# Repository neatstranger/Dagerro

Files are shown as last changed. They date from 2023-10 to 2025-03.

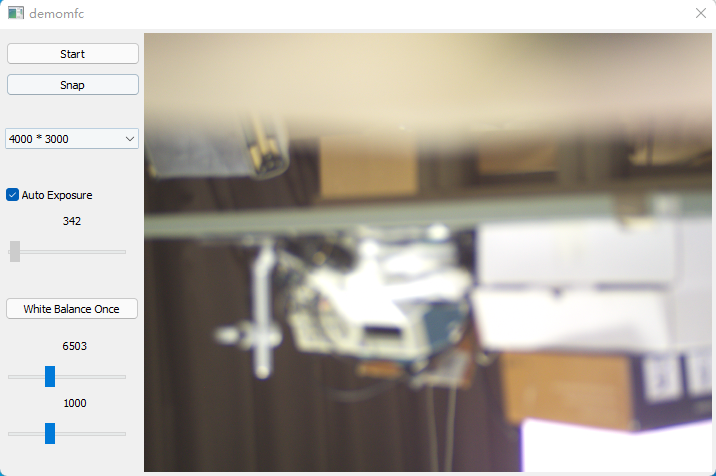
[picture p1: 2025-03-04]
toupcam/raw_sdk/doc/images/demomfc.png

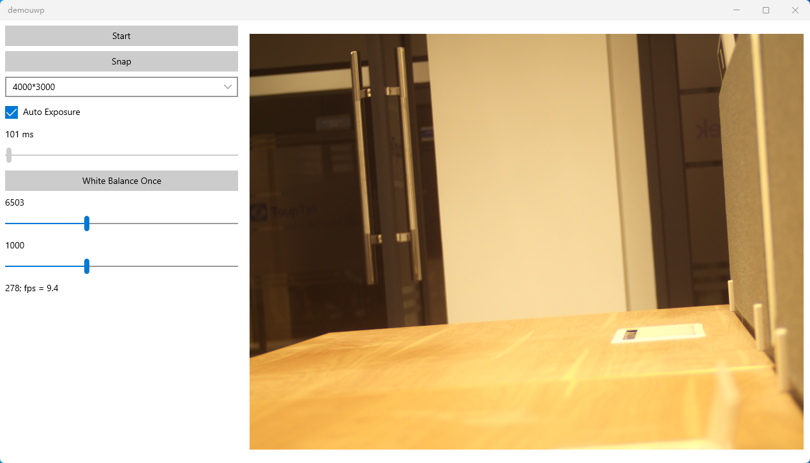
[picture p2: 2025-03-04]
toupcam/raw_sdk/doc/images/demouwp.png

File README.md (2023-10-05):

# Dagerro
>The first known attempt at astronomical photography was by Louis Jacques Mandé Daguerre, inventor of the daguerreotype process which bears his name, who attempted in 1839 to photograph the Moon. Tracking errors in guiding the telescope during the long exposure meant the photograph came out as an indistinct fuzzy spot. [Source](https://en.wikipedia.org/wiki/Astrophotography#:~:text=The%20first%20known%20attempt%20at,as%20an%20indistinct%20fuzzy%20spot.)

# Guide Timing
Some notes for myself as well as anyone reading. 
We need to move the steppers about 8 times per second and the Real Time Clock(RTC) doesn't allow for time resolution greater than 1 second. 
The RTC(DS3231) outputs 32,768 pulses per second on the 32K pin. We attach an interrupt to that pin with the following line.

`attachInterrupt(digitalPinToInterrupt(interruptPin), countCycles, CHANGE);`

Note the use of the `CHANGE` for activation. This means that we will capture one interrupt for each rise, and one for each fall.
With our second now divided up into 65,536 segments.

```
1 Degree = 60 ArcMinutes
1 ArcMinute = 60 ArcSeconds
1 Degree = 3600 ArcSeconds
```

How fast does the earth rotate? My previous assumption of ~1ArcSecond/Second~ is wrong. Let's do the math.
```
360° = 24 Hours
15° = 1 Hour or 60 Minutes or 3600 Seconds
1° or 3600 ArcSeconds = 4 Minutes or 240 Seconds
Math = 3600(ArcSeconds-Angle)/240 (Seconds-Time)
15 ArcSeconds(Angle) = 1 Second(Time)

```

The arduino receive exactly 1,658,880 pulses every 25.3125 seconds.
During this period of time, we need to take exactly 1500 steps.

python function to solve the problem.

```
x = 1
maxcount = 1500
xmult = 1105
ymult = 1107

while x <= maxcount:
    y = maxcount - x
    if (xmult*x)+(ymult*y) == 1658880:
        print(x)
        print(y)
        print((xmult*x) + (ymult*y))
    x+=1
```
I used this script, changing the values for xmult and ymult, until I got a result that looks like this:

```
810
690
1658880

```
Which means that if we take a step every 1105 interrupts, 810 times.
Followed by taking a step every 1107 interrupts, 690 times. 
We will have taken 1500 steps in exactly 25.3125 seconds. 

```
1500 Steps * 0.253125 ArcSeconds Per Step = 379.6875 ArcSeconds
379.6875 ArcSeconds / 25.3125 Seconds
15 ArcSeconds / Second
```

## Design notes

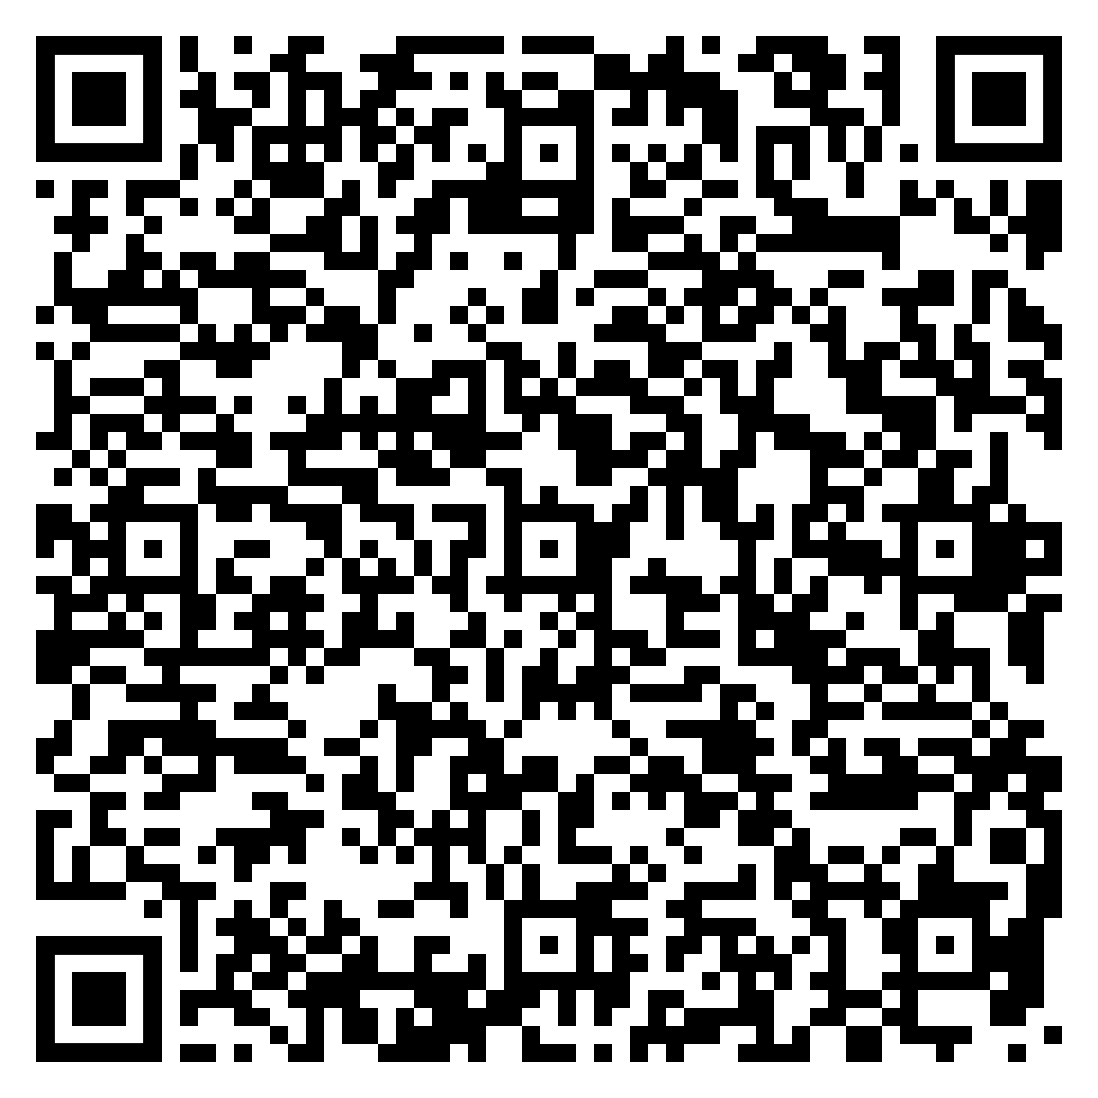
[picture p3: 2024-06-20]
Electronics/MountControl/assets/motor-drivers.png

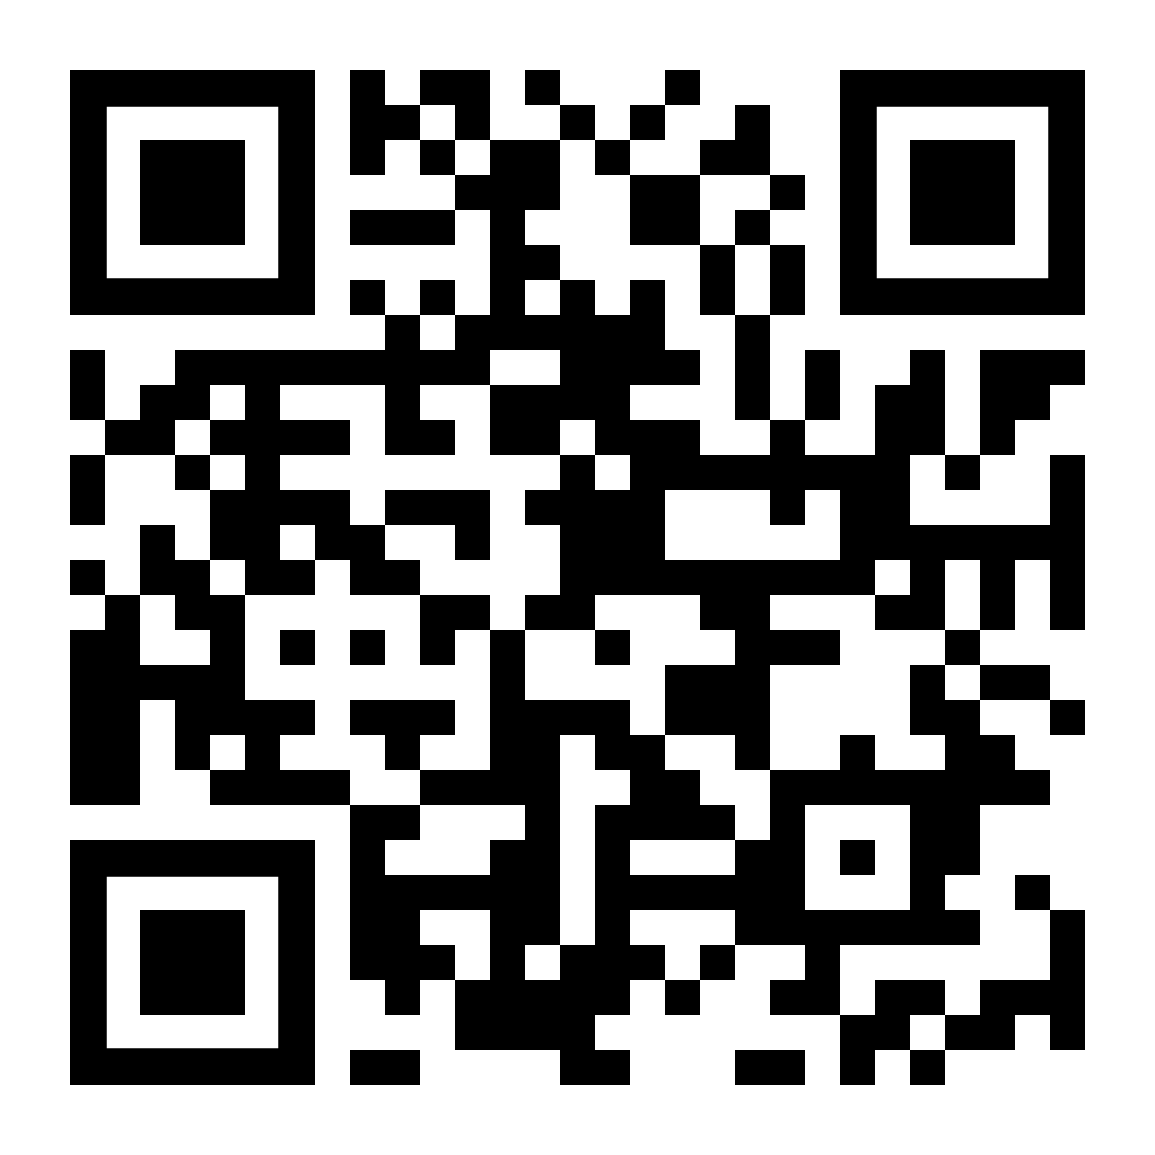
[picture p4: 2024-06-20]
Electronics/MountControl/assets/github-link.png

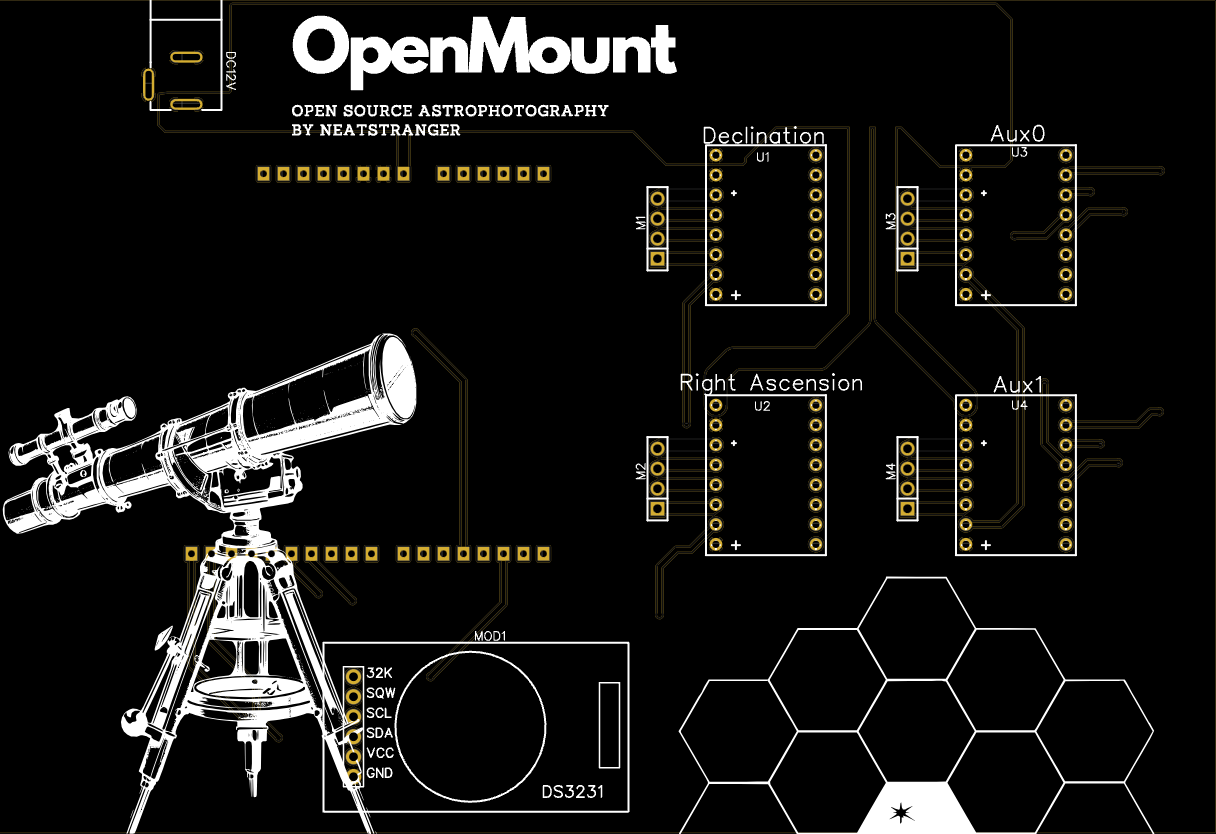
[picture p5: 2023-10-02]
Electronics/Top Side.png

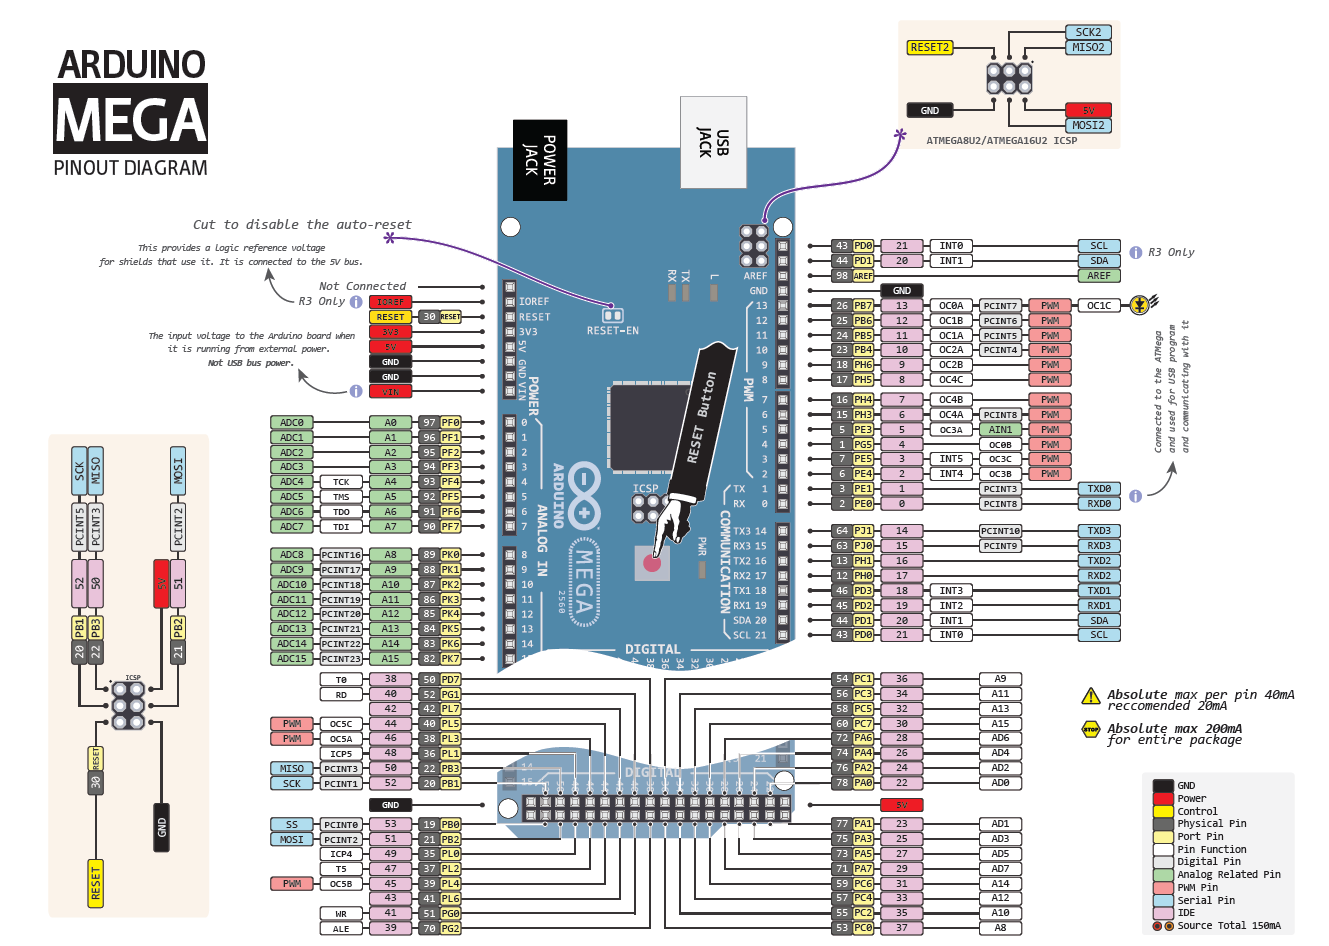
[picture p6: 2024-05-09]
arduino/pinout.png

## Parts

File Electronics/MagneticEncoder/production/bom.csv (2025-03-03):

Designator | Footprint | Quantity | Value | LCSC Part #
C1 | 1206 | 1 | 0.1u
J1, J5 | PinHeader_1x02_P2.54mm_Vertical | 2 | Conn_01x02_Pin
J2, J4 | PinHeader_1x01_P2.54mm_Vertical | 2 | Conn_01x01_Pin
J3 | PinHeader_1x03_P2.54mm_Vertical | 1 | Conn_01x03_Pin
U1 | QFN-16_L3.0-W3.0-P0.50-TL-EP1.7 | 1 | MT6701QT-STD_C2913974 | C2913974

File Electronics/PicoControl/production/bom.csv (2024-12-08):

Designator | Footprint | Quantity | Value | LCSC Part #
C1, C2, C8, C9 | 1206 | 4 | 2.2u | C170101
C10, C3 | 1206 | 2 | 0.1u | C56392
C11, C4 | 1206 | 2 | 6800p | C2760541
C12, C5 | 1206 | 2 | 39p | C5186878
C13, C14, C6, C7 | 1206 | 4 | 47u | C94034
C15 | 1206 | 1 | 0.1u
CN1 | CONN-TH_2P-P5.00_WJ500V-5.08-2P | 1 | Battery | C8465
CN2 | CONN-TH_5P-P5.08_DIBO_DB128V-5.08-5P-GN-S | 1 | EQ | C2927513
CN3 | CONN-TH_5P-P5.08_DIBO_DB128V-5.08-5P-GN-S | 1 | DEC | C2927513
CN4 | CONN-TH_5P-P5.08_DIBO_DB128V-5.08-5P-GN-S | 1 | FOCUS | C2927513
CN5 | CONN-TH_2P-P5.00_WJ500V-5.08-2P | 1 | Camera | C8465
D1, D2 | SMC_L7.1-W6.2-LS8.1-RD | 2 | B560C-13-F | C85100
J1 | PinHeader_1x03_P2.54mm_Vertical | 1 | Conn_01x03_Pin
J2 | PinHeader_1x03_P2.54mm_Vertical | 1 | Conn_01x03_Socket
J3, J5 | PinHeader_1x03_P2.54mm_Horizontal | 2 | Conn_01x03_Pin
J4 | PinHeader_1x06_P2.54mm_Vertical | 1 | Conn_01x06_Pin
L1, L2 | IND-SMD_L11.5-W10.0_FXL1040 | 2 | FXL1040-8R2-M | C167232
R1, R5 | 1206 | 2 | 162k | C22815
R10, R9 | 1206 | 2 | 5k
R11 | 1206 | 1 | 10k
R12 | 1206 | 1 | 100k
R2, R6 | 1206 | 2 | 13k | C445658
R3 | 1206 | 1 | 53.6k | C21398
R4, R8 | 1206 | 2 | 10.2k | C217771
R7 | 1206 | 1 | 81.6k | C21398
U1, U2 | SOIC-8_L5.0-W4.0-P1.27-LS6.0-BL-EP2.0 | 2 | TPS54360BDDAR | C524806
U3 | SOIC-14_L10.1-W5.0-P1.27-LS7.4-BL | 1 | RX8025T-UB | C17353
U4 | RPi_Pico_SMD_TH | 1 | Pico
USB1 | USB-A-TH_USB-231-ARY | 1 | Pi-Power | C720525

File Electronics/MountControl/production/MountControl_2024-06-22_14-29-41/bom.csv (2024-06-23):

Designator | Footprint | Quantity | Value | LCSC Part #
12V-Current-Sense1, 24V-Current-Sense1, DEC-Current-Sense1, FOCUS-Current-Sense1, RA-Current-Sense1 | RES-SMD_L6.4-W3.2-R2512 | 5 | HOJLR2512-3W-1MR-1% | C2903470
12V-Input1, 24V-Input1, Thermistor1, Thermistor2, Thermistor3, Thermistor4, Thermistor5 | CONN-TH_2P-P5.00_WJ500V-5.08-2P | 7 | WJ500V-5.08-2P-14-00A | C8465
A1 | Arduino_Mega2560_R3_Shield | 1 | Arduino_Mega2560_R3_Shield
DEC-Hall-Effect1, RA-Hall-Effect1 | CONN-TH_XY303V-3.81-3P | 2 | XY303V-3.81-3P | C557684
DEC-Motor1, FOCUS-Motor1, Filter-Wheel1, RA-Motor1 | CONN-TH_5P-P5.08_DIBO_DB128V-5.08-5P-GN-S | 4 | DB128V-5.08-5P-GN-S | C2927513

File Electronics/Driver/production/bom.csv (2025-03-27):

Designator | Footprint | Quantity | Value | LCSC Part #
C1 | 1206 | 1 | 100u
C2 | 1206 | 1 | 0.01u
C3 | 1206 | 1 | 0.47u
C4, C5, C6, C7 | 1206 | 4 | 0.1u
J1, J2 | PinSocket_1x10_P2.54mm_Vertical | 2 | Conn_01x10_Pin
U1 | WQFN-16_L3.0-W3.0-P0.50-BL-EP1.7 | 1 | DRV8428RTER | C2857955
U4, U5 | SOT-23-5_L3.0-W1.7-P0.95-LS2.8-BL | 2 | SN74LVC1G125DBVR | C23654
U6 | SOT-23-6_L2.9-W1.6-P0.95-LS2.8-BL | 1 | MCP4725A0T-E/CH | C144198

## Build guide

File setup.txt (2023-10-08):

#Install PiVariety Cam Drivers
wget -O install_pivariety_pkgs.sh https://github.com/ArduCAM/Arducam-Pivariety-V4L2-Driver/releases/download/install_script/install_pivariety_pkgs.sh
chmod +x install_pivariety_pkgs.sh

./install_pivariety_pkgs.sh -p libcamera_dev

./install_pivariety_pkgs.sh -p libcamera_apps

./install_pivariety_pkgs.sh -p kernel_driver

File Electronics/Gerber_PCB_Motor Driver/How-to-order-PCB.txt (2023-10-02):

How to Order PCB

Please refer to:
https://docs.easyeda.com/en/PCB/Order-PCB

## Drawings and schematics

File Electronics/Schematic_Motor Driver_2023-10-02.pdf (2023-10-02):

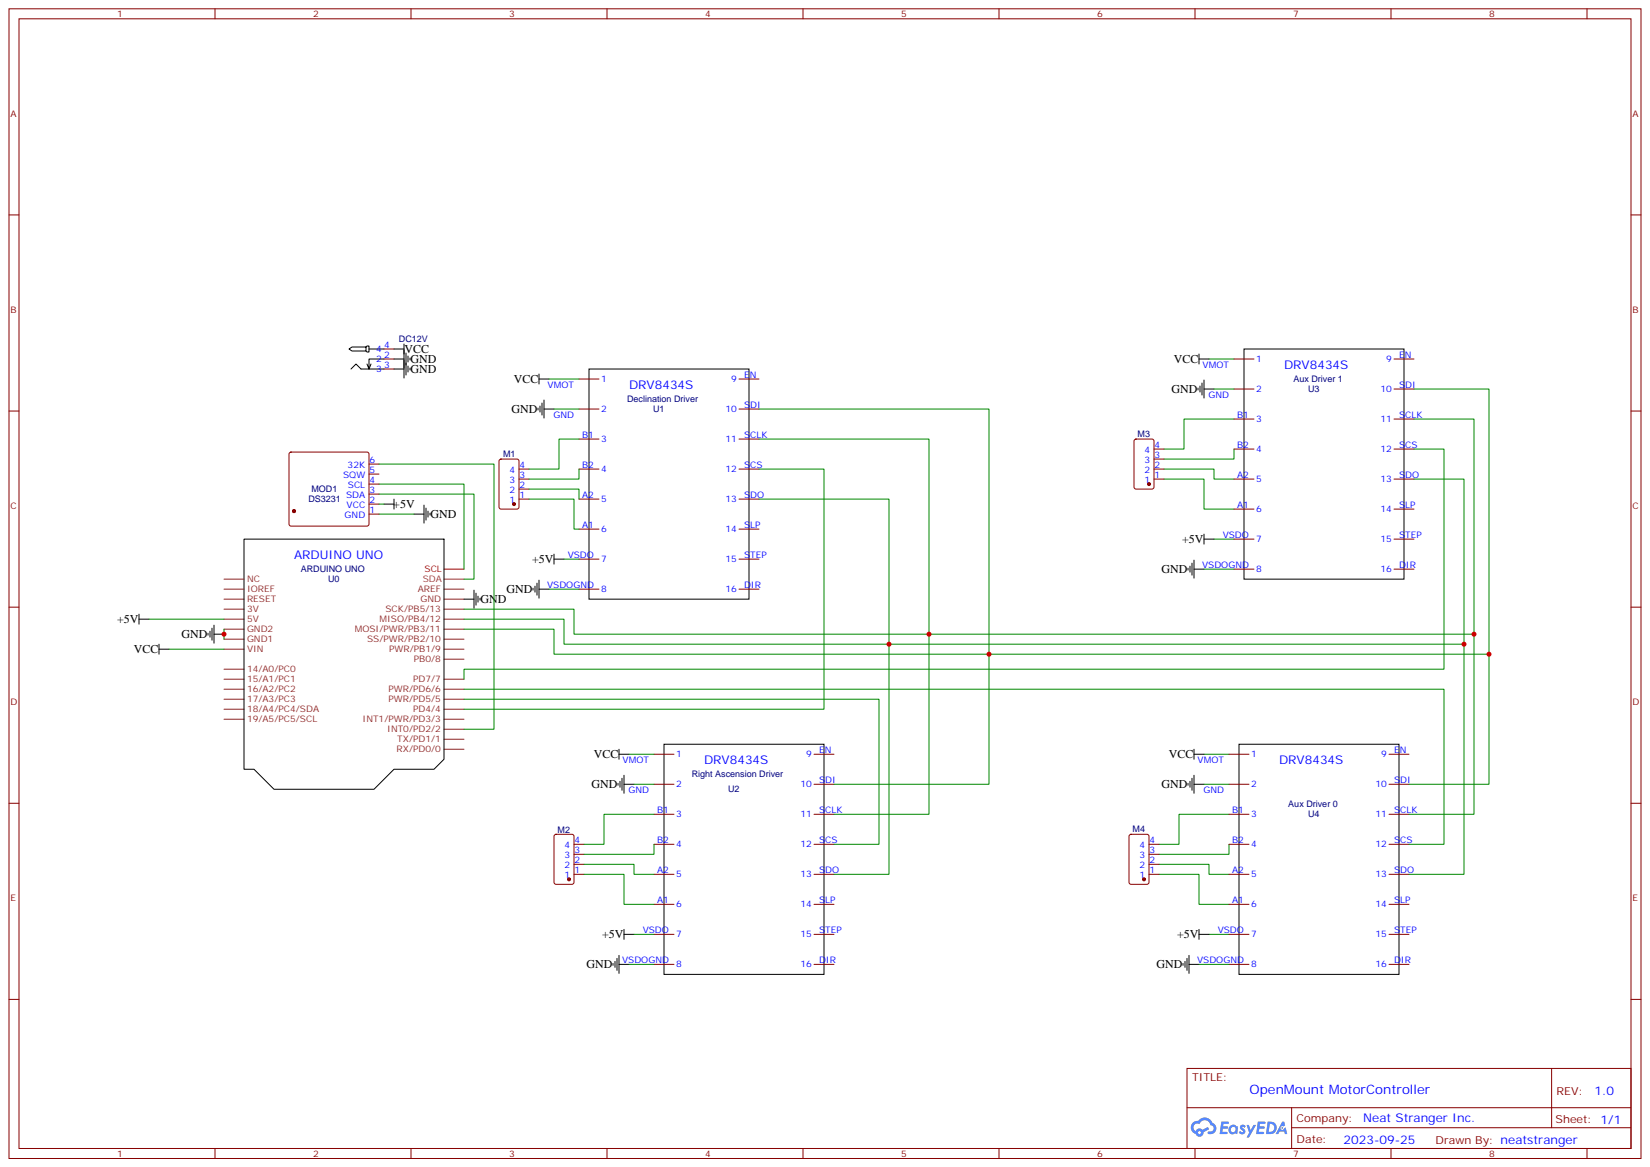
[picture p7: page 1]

Company: Neat Stranger Inc.

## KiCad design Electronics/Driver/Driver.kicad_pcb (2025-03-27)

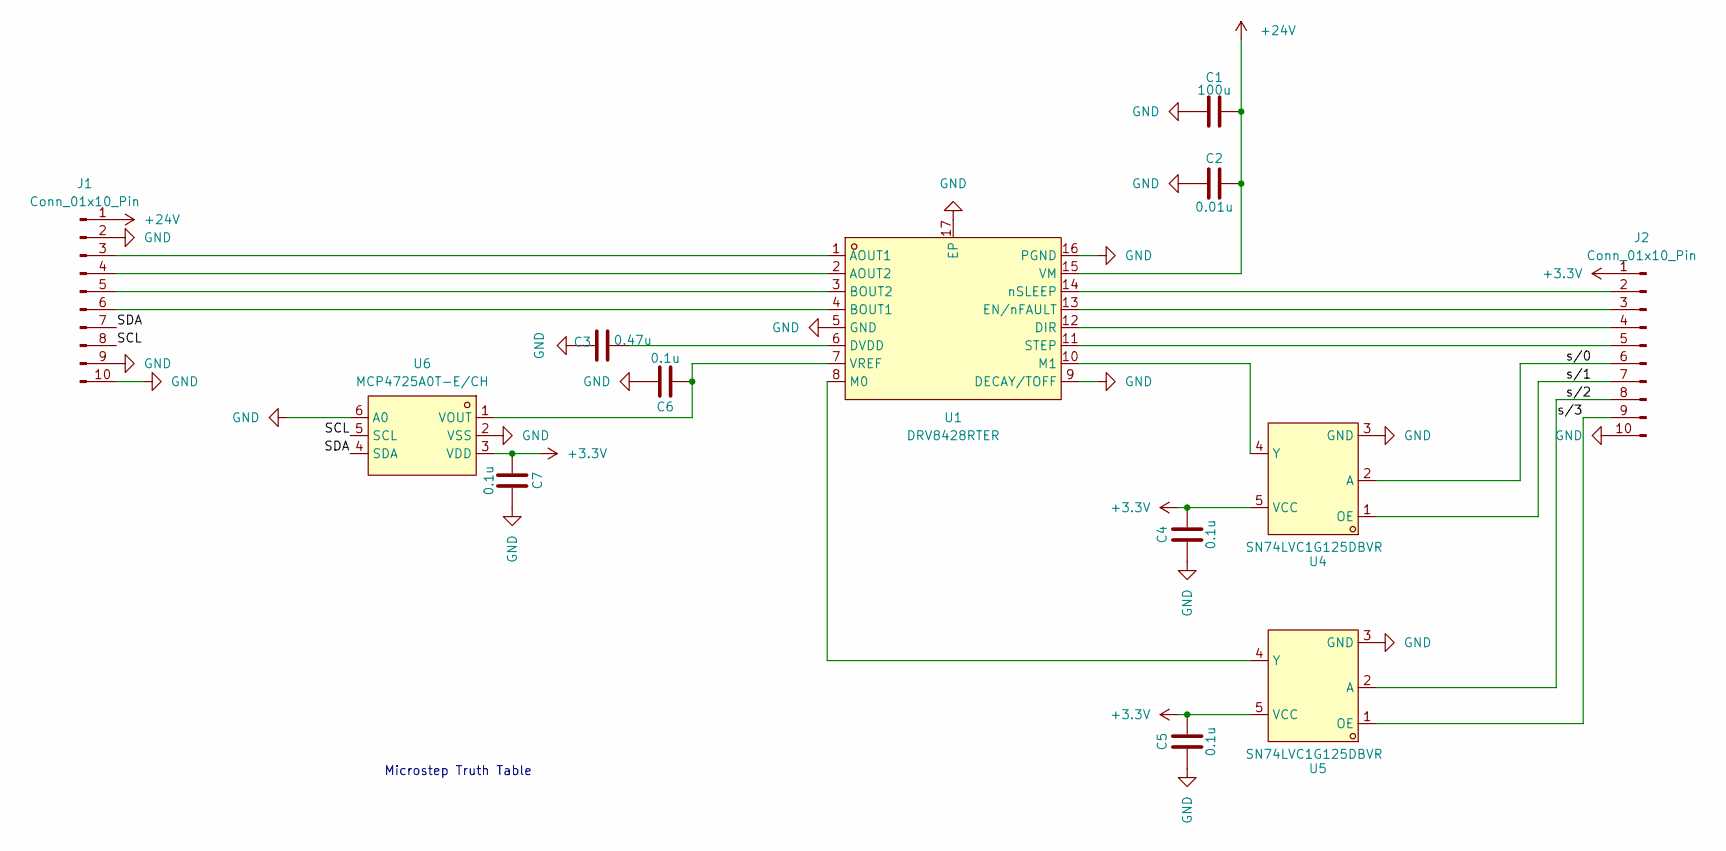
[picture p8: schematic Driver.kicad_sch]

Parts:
C1: 100u; C_1206_3216Metric_Pad1.33x1.80mm_HandSolder
C2: 0.01u; C_1206_3216Metric_Pad1.33x1.80mm_HandSolder
C3: 0.47u; C_1206_3216Metric_Pad1.33x1.80mm_HandSolder
C4, C5, C6, C7: 0.1u; C_1206_3216Metric_Pad1.33x1.80mm_HandSolder
J1, J2: Conn_01x10_Pin; PinSocket_1x10_P2.54mm_Vertical
U1: DRV8428RTER; WQFN-16_L3.0-W3.0-P0.50-BL-EP1.7; LCSC Part C2857955
U4, U5: SN74LVC1G125DBVR; SOT-23-5_L3.0-W1.7-P0.95-LS2.8-BL; LCSC Part C23654
U6: MCP4725A0T-E/CH; SOT-23-6_L2.9-W1.6-P0.95-LS2.8-BL; LCSC Part C144198

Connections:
+3.3V: C4.2, C5.2, C7.2, J2.1, U4.5 (VCC), U5.5 (VCC), U6.3 (VDD)
+24V: C1.2, C2.2, J1.1, U1.15 (VM)
/SCL: J1.8, U6.5 (SCL)
/SDA: J1.7, U6.4 (SDA)
GND: C1.1, C2.1, C3.1, C4.1, C5.1, C6.1, C7.1, J1.2, J1.9, J1.10, J2.10, U1.5 (GND), U1.9 (DECAY/TOFF), U1.16 (PGND), U1.17 (EP), U4.3 (GND), U5.3 (GND), U6.2 (VSS), U6.6 (A0)
unnamed: J1.3, U1.1 (AOUT1)
unnamed: J1.4, U1.2 (AOUT2)
unnamed: J1.5, U1.3 (BOUT2)
unnamed: J1.6, U1.4 (BOUT1)
unnamed: J2.2, U1.14 (nSLEEP)
unnamed: J2.3, U1.13 (EN/nFAULT)
unnamed: J2.4, U1.12 (DIR)
unnamed: J2.5, U1.11 (STEP)
unnamed: J2.6, U4.2 (A)
unnamed: J2.7, U4.1 (OE)
unnamed: J2.8, U5.2 (A)
unnamed: J2.9, U5.1 (OE)
unnamed: C3.2, U1.6 (DVDD)
unnamed: U1.8 (M0), U5.4 (Y)
unnamed: U1.10 (M1), U4.4 (Y)
unnamed: C6.2, U1.7 (VREF), U6.1 (VOUT)

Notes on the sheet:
Microstep Truth Table

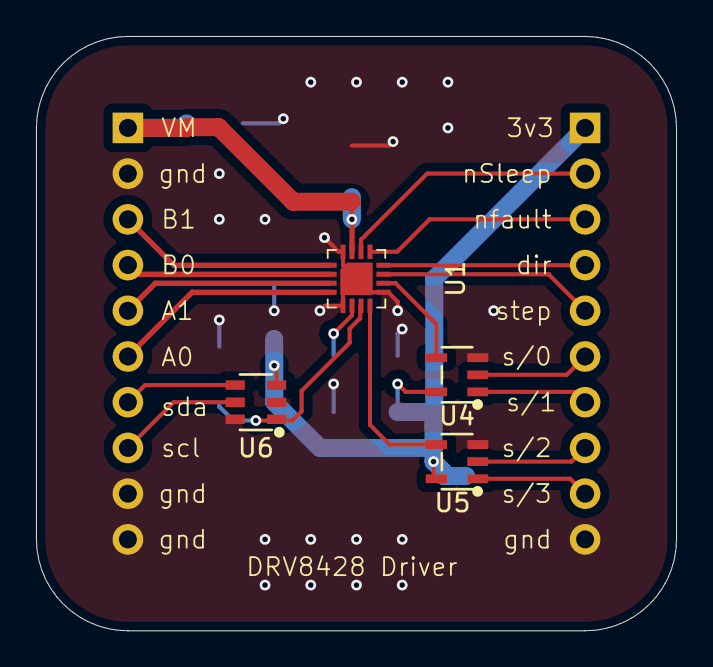
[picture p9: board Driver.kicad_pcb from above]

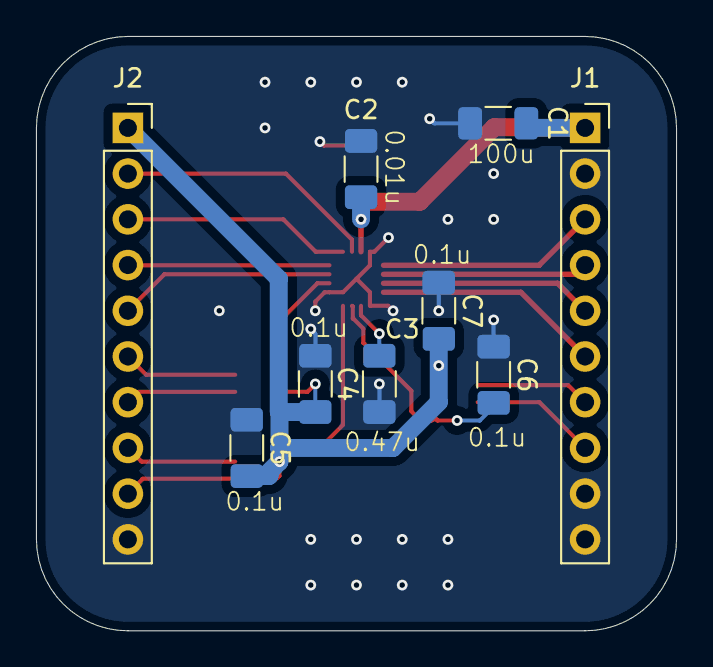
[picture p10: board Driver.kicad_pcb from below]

Board: 2 copper layers, 35.6 x 33.0 mm, 13 parts (9 on the bottom side), 21 nets.

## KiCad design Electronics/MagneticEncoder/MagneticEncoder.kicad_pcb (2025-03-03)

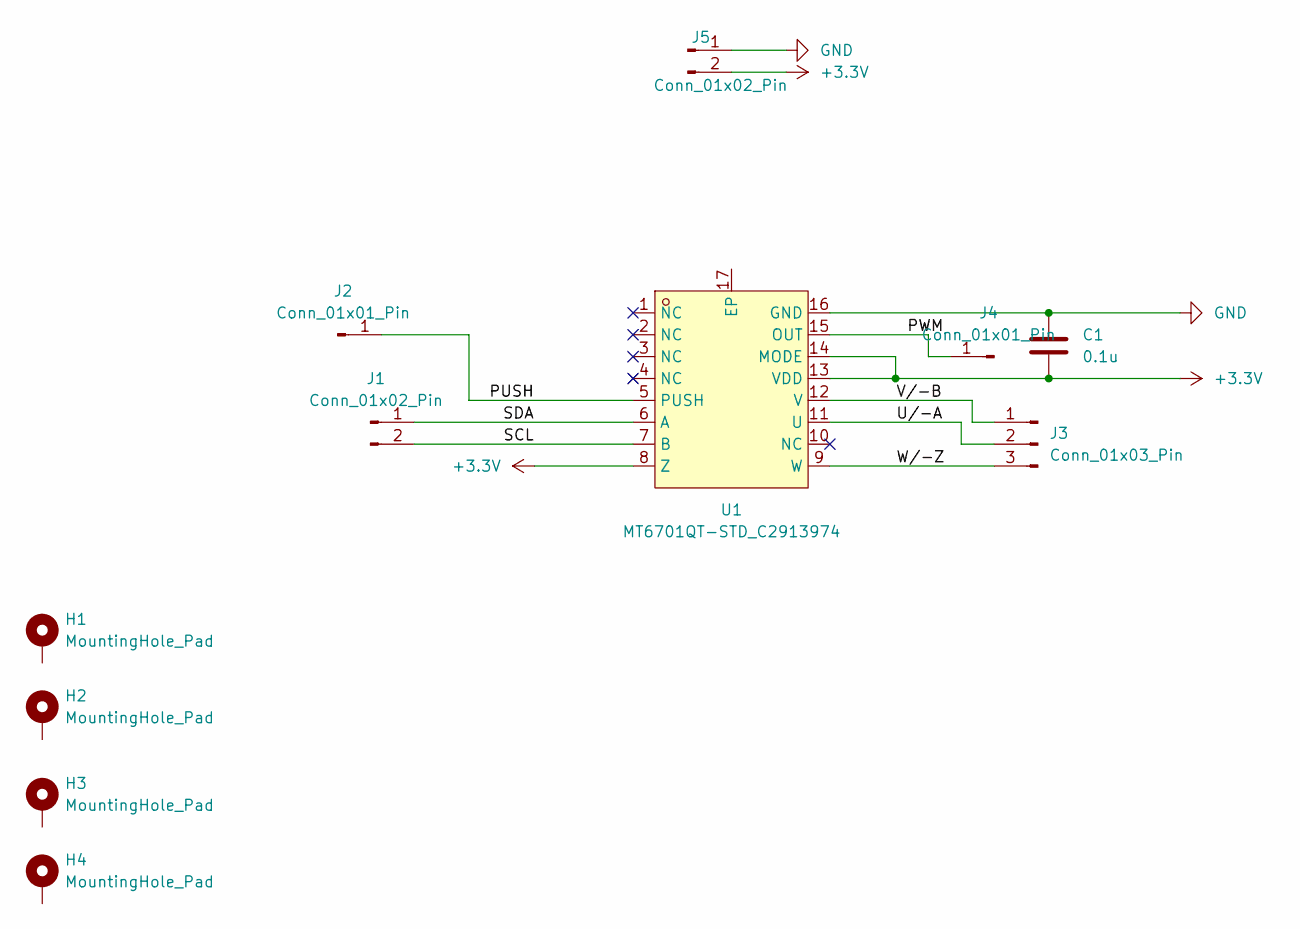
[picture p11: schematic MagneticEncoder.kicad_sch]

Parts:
C1: 0.1u; C_1206_3216Metric_Pad1.33x1.80mm_HandSolder
H1, H2, H3, H4: MountingHole_Pad; MountingHole_3.2mm_M3_DIN965_Pad_TopBottom
J1, J5: Conn_01x02_Pin; PinHeader_1x02_P2.54mm_Vertical
J2, J4: Conn_01x01_Pin; PinHeader_1x01_P2.54mm_Vertical
J3: Conn_01x03_Pin; PinHeader_1x03_P2.54mm_Vertical
U1: MT6701QT-STD_C2913974; QFN-16_L3.0-W3.0-P0.50-TL-EP1.7; LCSC Part C2913974

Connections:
+3.3V: C1.2, J5.2, U1.8 (Z), U1.13 (VDD), U1.14 (MODE)
/PUSH: J2.1, U1.5 (PUSH)
/PWM: J4.1, U1.15 (OUT)
/SCL: J1.2, U1.7 (B)
/SDA: J1.1, U1.6 (A)
/U/-A: J3.2, U1.11 (U)
/V/-B: J3.1, U1.12 (V)
/W/-Z: J3.3, U1.9 (W)
GND: C1.1, J5.1, U1.16 (GND)

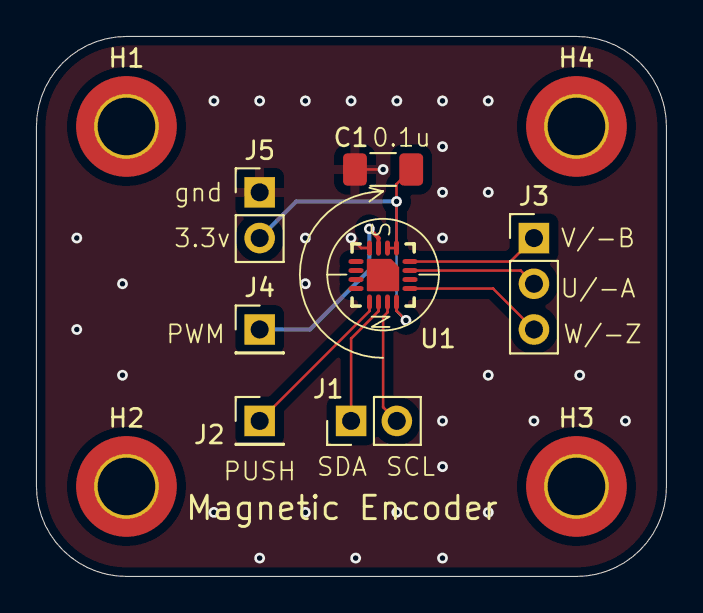
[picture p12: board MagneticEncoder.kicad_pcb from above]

Board: 2 copper layers, 35.0 x 30.0 mm, 11 parts (0 on the bottom side), 9 nets.

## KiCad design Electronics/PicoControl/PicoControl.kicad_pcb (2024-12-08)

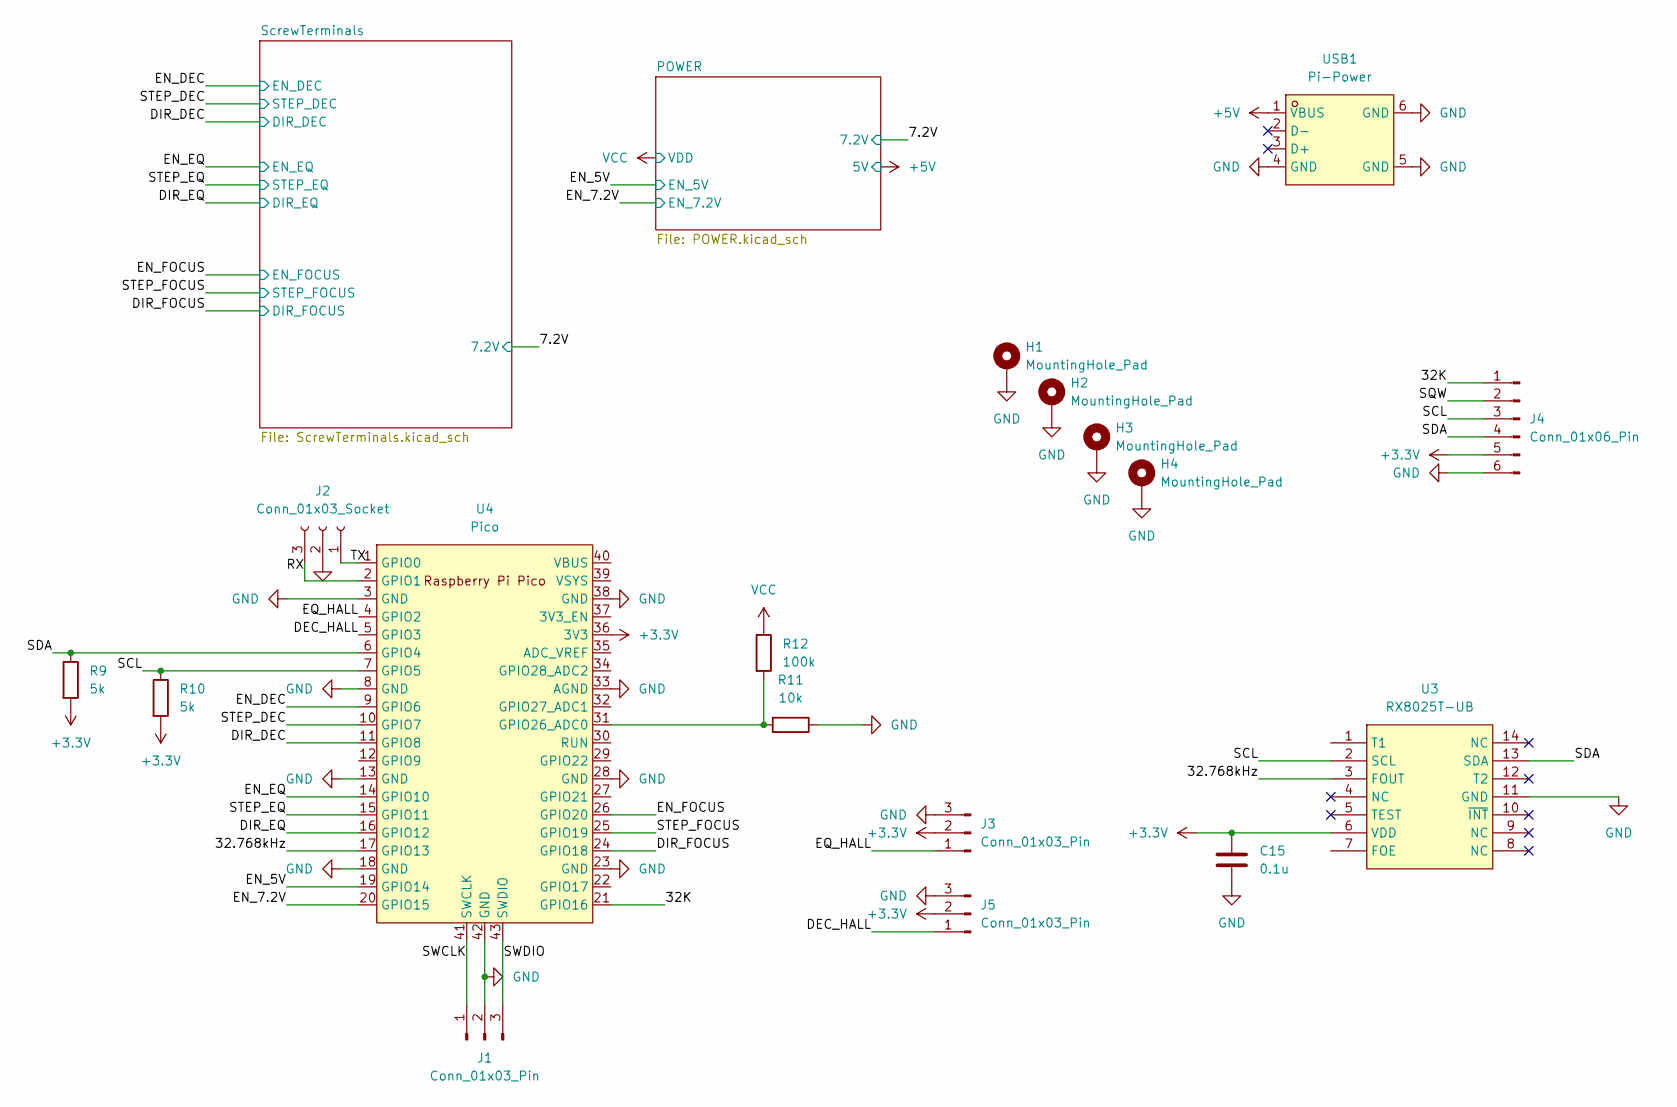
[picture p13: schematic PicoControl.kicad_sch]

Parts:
C15: 0.1u; C_1206_3216Metric_Pad1.33x1.80mm_HandSolder
H1, H2, H3, H4: MountingHole_Pad; MountingHole_5.3mm_M5_DIN965_Pad
J1: Conn_01x03_Pin; PinHeader_1x03_P2.54mm_Vertical
J2: Conn_01x03_Socket; PinHeader_1x03_P2.54mm_Vertical
J3, J5: Conn_01x03_Pin; PinHeader_1x03_P2.54mm_Horizontal
J4: Conn_01x06_Pin; PinHeader_1x06_P2.54mm_Vertical
R9, R10: 5k; R_1206_3216Metric_Pad1.30x1.75mm_HandSolder
R11: 10k; R_1206_3216Metric_Pad1.30x1.75mm_HandSolder
R12: 100k; R_1206_3216Metric_Pad1.30x1.75mm_HandSolder
U3: RX8025T-UB; SOIC-14_L10.1-W5.0-P1.27-LS7.4-BL; LCSC Part C17353
U4: Pico; RPi_Pico_SMD_TH
USB1: Pi-Power; USB-A-TH_USB-231-ARY; LCSC Part C720525

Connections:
+3.3V: C15.2, J3.2, J4.5, J5.2, R9.2, R10.2, U3.6 (VDD), U4.36 (3V3)
+5V: USB1.1 (VBUS); also elsewhere on the board
/32.768kHz: U3.3 (FOUT), U4.17 (GPIO13)
/32K: J4.1, U4.21 (GPIO16)
/DEC_HALL: J5.1, U4.5 (GPIO3)
/DIR_DEC: U4.11 (GPIO8); also elsewhere on the board
/DIR_EQ: U4.16 (GPIO12); also elsewhere on the board
/DIR_FOCUS: U4.24 (GPIO18); also elsewhere on the board
/EN_5V: U4.19 (GPIO14); also elsewhere on the board
/EN_7.2V: U4.20 (GPIO15); also elsewhere on the board
/EN_DEC: U4.9 (GPIO6); also elsewhere on the board
/EN_EQ: U4.14 (GPIO10); also elsewhere on the board
/EN_FOCUS: U4.26 (GPIO20); also elsewhere on the board
/EQ_HALL: J3.1, U4.4 (GPIO2)
/RX: J2.3, U4.2 (GPIO1)
/SCL: J4.3, R10.1, U3.2 (SCL), U4.7 (GPIO5)
/SDA: J4.4, R9.1, U3.13 (SDA), U4.6 (GPIO4)
/SQW: J4.2
/STEP_DEC: U4.10 (GPIO7); also elsewhere on the board
/STEP_EQ: U4.15 (GPIO11); also elsewhere on the board
/STEP_FOCUS: U4.25 (GPIO19); also elsewhere on the board
/SWCLK: J1.1, U4.41 (SWCLK)
/SWDIO: J1.3, U4.43 (SWDIO)
/TX: J2.1, U4.1 (GPIO0)
GND: C15.1, H1.1, H2.1, H3.1, H4.1, J1.2, J2.2, J3.3, J4.6, J5.3, R11.1, U3.11 (GND), U4.3 (GND), U4.8 (GND), U4.13 (GND), U4.18 (GND), U4.23 (GND), U4.28 (GND), U4.33 (AGND), U4.38 (GND), U4.42 (GND), USB1.4 (GND), USB1.5 (GND), USB1.6 (GND); also elsewhere on the board
unnamed: R11.2, R12.2, U4.31 (GPIO26_ADC0)
VCC: R12.1; also elsewhere on the board

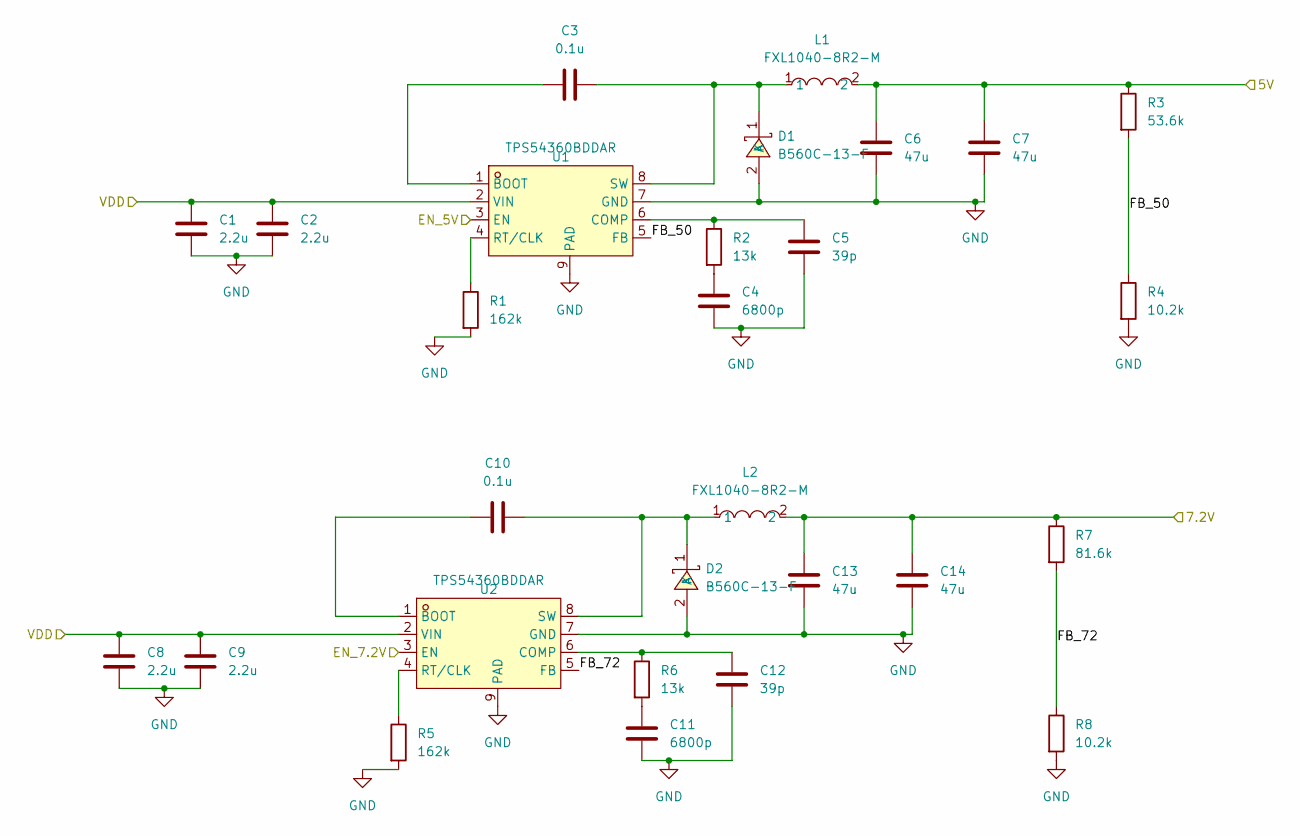
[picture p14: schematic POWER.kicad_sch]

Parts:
C1, C2, C8, C9: 2.2u; C_1206_3216Metric; LCSC Part C170101
C3, C10: 0.1u; C_1206_3216Metric_Pad1.33x1.80mm_HandSolder; LCSC Part C56392
C4, C11: 6800p; C_1206_3216Metric_Pad1.33x1.80mm_HandSolder; LCSC Part C2760541
C5, C12: 39p; C_1206_3216Metric_Pad1.33x1.80mm_HandSolder; LCSC Part C5186878
C6, C7, C13, C14: 47u; C_1206_3216Metric; LCSC Part C94034
D1, D2: B560C-13-F; SMC_L7.1-W6.2-LS8.1-RD; LCSC Part C85100
L1, L2: FXL1040-8R2-M; IND-SMD_L11.5-W10.0_FXL1040; LCSC Part C167232
R1, R5: 162k; R_1206_3216Metric_Pad1.30x1.75mm_HandSolder; LCSC Part C22815
R2, R6: 13k; R_1206_3216Metric_Pad1.30x1.75mm_HandSolder; LCSC Part C445658
R3: 53.6k; R_1206_3216Metric_Pad1.30x1.75mm_HandSolder; LCSC Part C21398
R4, R8: 10.2k; R_1206_3216Metric_Pad1.30x1.75mm_HandSolder; LCSC Part C217771
R7: 81.6k; R_1206_3216Metric_Pad1.30x1.75mm_HandSolder; LCSC Part C21398
U1, U2: TPS54360BDDAR; SOIC-8_L5.0-W4.0-P1.27-LS6.0-BL-EP2.0; LCSC Part C524806

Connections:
+5V: C6.1, C7.1, L1.2, R3.1; also elsewhere on the board
/7.2V: C13.1, C14.1, L2.2, R7.1; also elsewhere on the board
/EN_5V: U1.3 (EN); also elsewhere on the board
/EN_7.2V: U2.3 (EN); also elsewhere on the board
/POWER/FB_50: R3.2, R4.1, U1.5 (FB)
/POWER/FB_72: R7.2, R8.1, U2.5 (FB)
GND: C1.2, C2.2, C4.2, C5.2, C6.2, C7.2, C8.2, C9.2, C11.2, C12.2, C13.2, C14.2, D1.2 (A), D2.2 (A), R1.2, R4.2, R5.2, R8.2, U1.7 (GND), U1.9 (PAD), U2.7 (GND), U2.9 (PAD); also elsewhere on the board
unnamed: C4.1, R2.2
unnamed: C11.1, R6.2
unnamed: C3.2, D1.1 (K), L1.1, U1.8 (SW)
unnamed: C10.2, D2.1 (K), L2.1, U2.8 (SW)
unnamed: C3.1, U1.1 (BOOT)
unnamed: C5.1, R2.1, U1.6 (COMP)
unnamed: R1.1, U1.4 (RT/CLK)
unnamed: C10.1, U2.1 (BOOT)
unnamed: C12.1, R6.1, U2.6 (COMP)
unnamed: R5.1, U2.4 (RT/CLK)
VCC: C1.1, C2.1, C8.1, C9.1, U1.2 (VIN), U2.2 (VIN); also elsewhere on the board

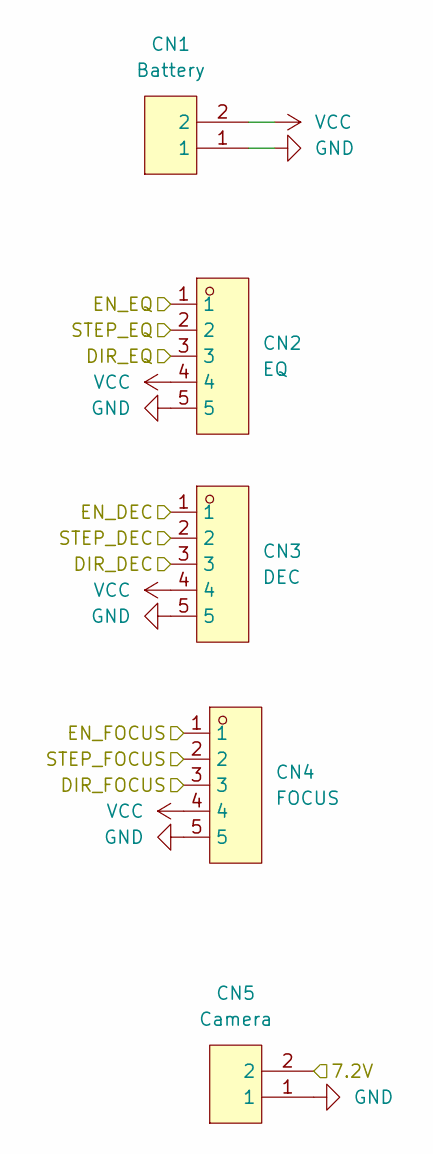
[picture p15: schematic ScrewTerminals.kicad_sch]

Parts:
CN1: Battery; CONN-TH_2P-P5.00_WJ500V-5.08-2P; LCSC Part C8465
CN2: EQ; CONN-TH_5P-P5.08_DIBO_DB128V-5.08-5P-GN-S; LCSC Part C2927513
CN3: DEC; CONN-TH_5P-P5.08_DIBO_DB128V-5.08-5P-GN-S; LCSC Part C2927513
CN4: FOCUS; CONN-TH_5P-P5.08_DIBO_DB128V-5.08-5P-GN-S; LCSC Part C2927513
CN5: Camera; CONN-TH_2P-P5.00_WJ500V-5.08-2P; LCSC Part C8465

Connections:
/7.2V: CN5.2; also elsewhere on the board
/DIR_DEC: CN3.3; also elsewhere on the board
/DIR_EQ: CN2.3; also elsewhere on the board
/DIR_FOCUS: CN4.3; also elsewhere on the board
/EN_DEC: CN3.1; also elsewhere on the board
/EN_EQ: CN2.1; also elsewhere on the board
/EN_FOCUS: CN4.1; also elsewhere on the board
/STEP_DEC: CN3.2; also elsewhere on the board
/STEP_EQ: CN2.2; also elsewhere on the board
/STEP_FOCUS: CN4.2; also elsewhere on the board
GND: CN1.1, CN2.5, CN3.5, CN4.5, CN5.1; also elsewhere on the board
VCC: CN1.2, CN2.4, CN3.4, CN4.4; also elsewhere on the board

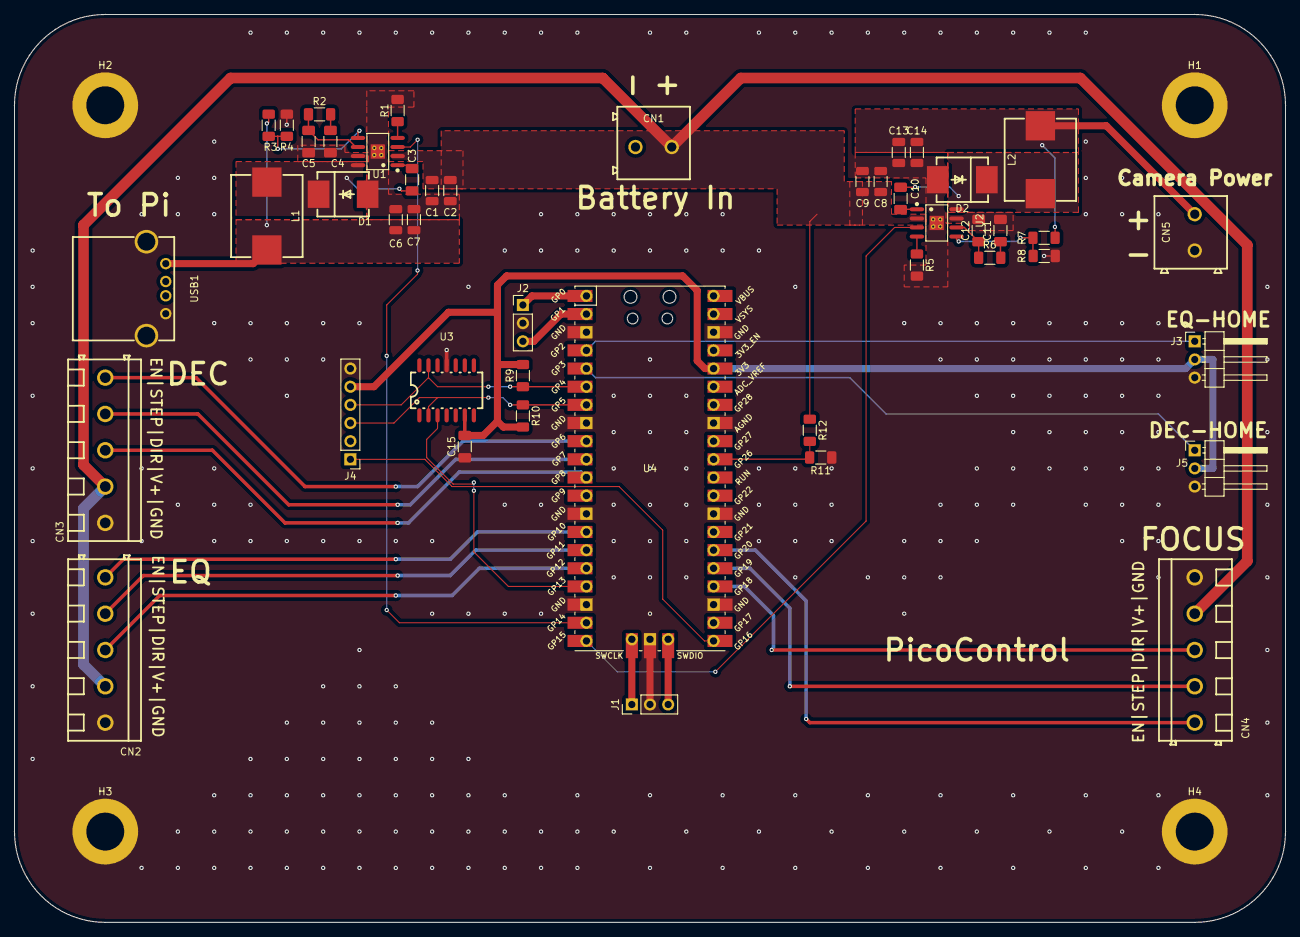
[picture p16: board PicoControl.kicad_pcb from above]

Board: 2 copper layers, 177.8 x 127.0 mm, 50 parts (0 on the bottom side), 39 nets.

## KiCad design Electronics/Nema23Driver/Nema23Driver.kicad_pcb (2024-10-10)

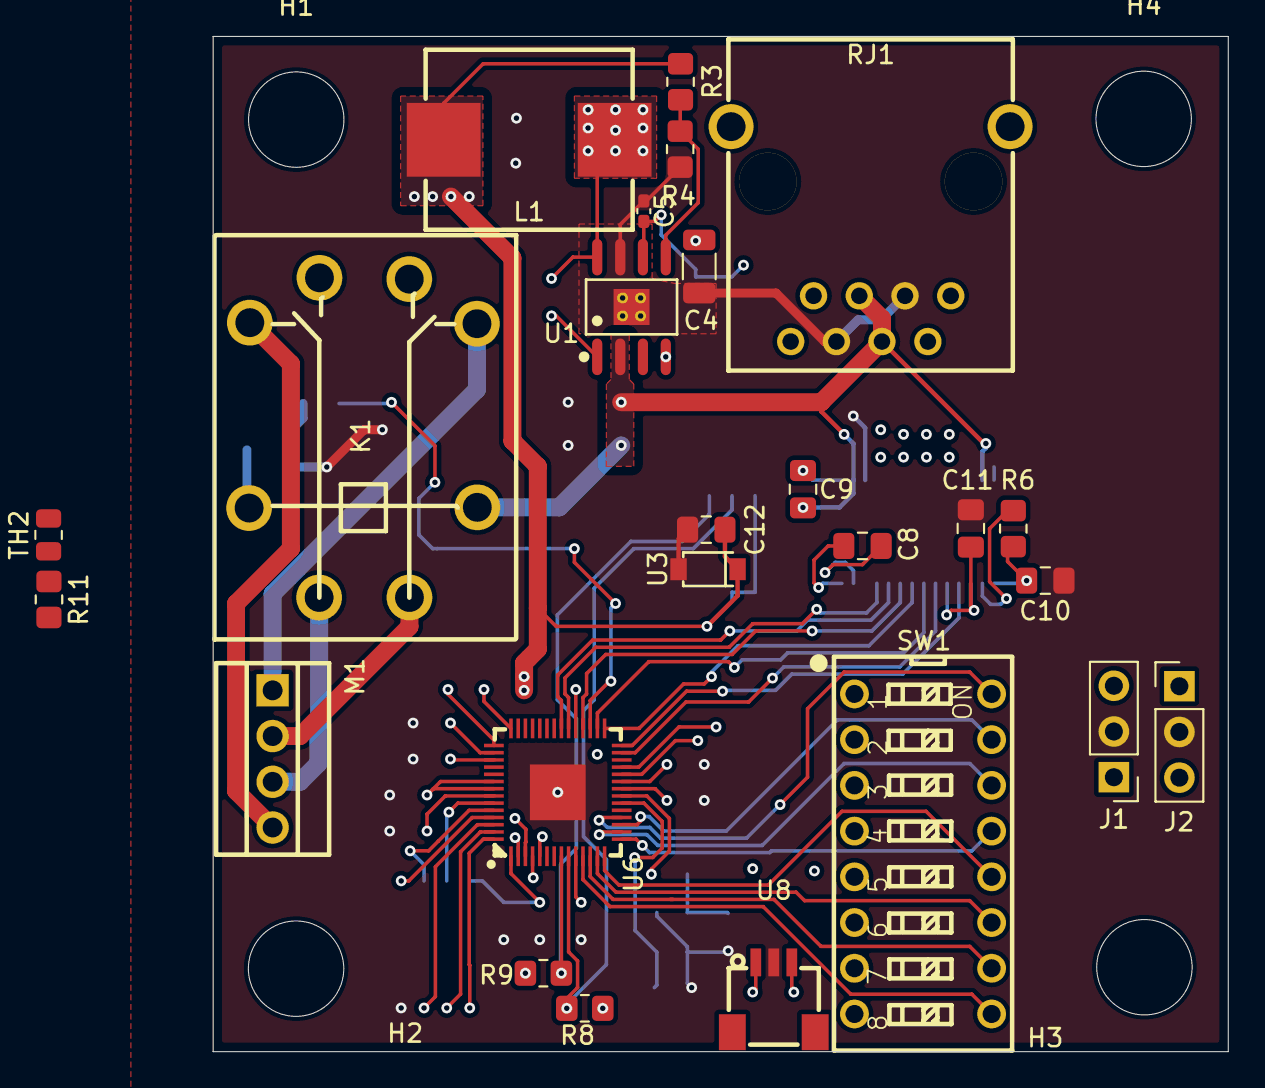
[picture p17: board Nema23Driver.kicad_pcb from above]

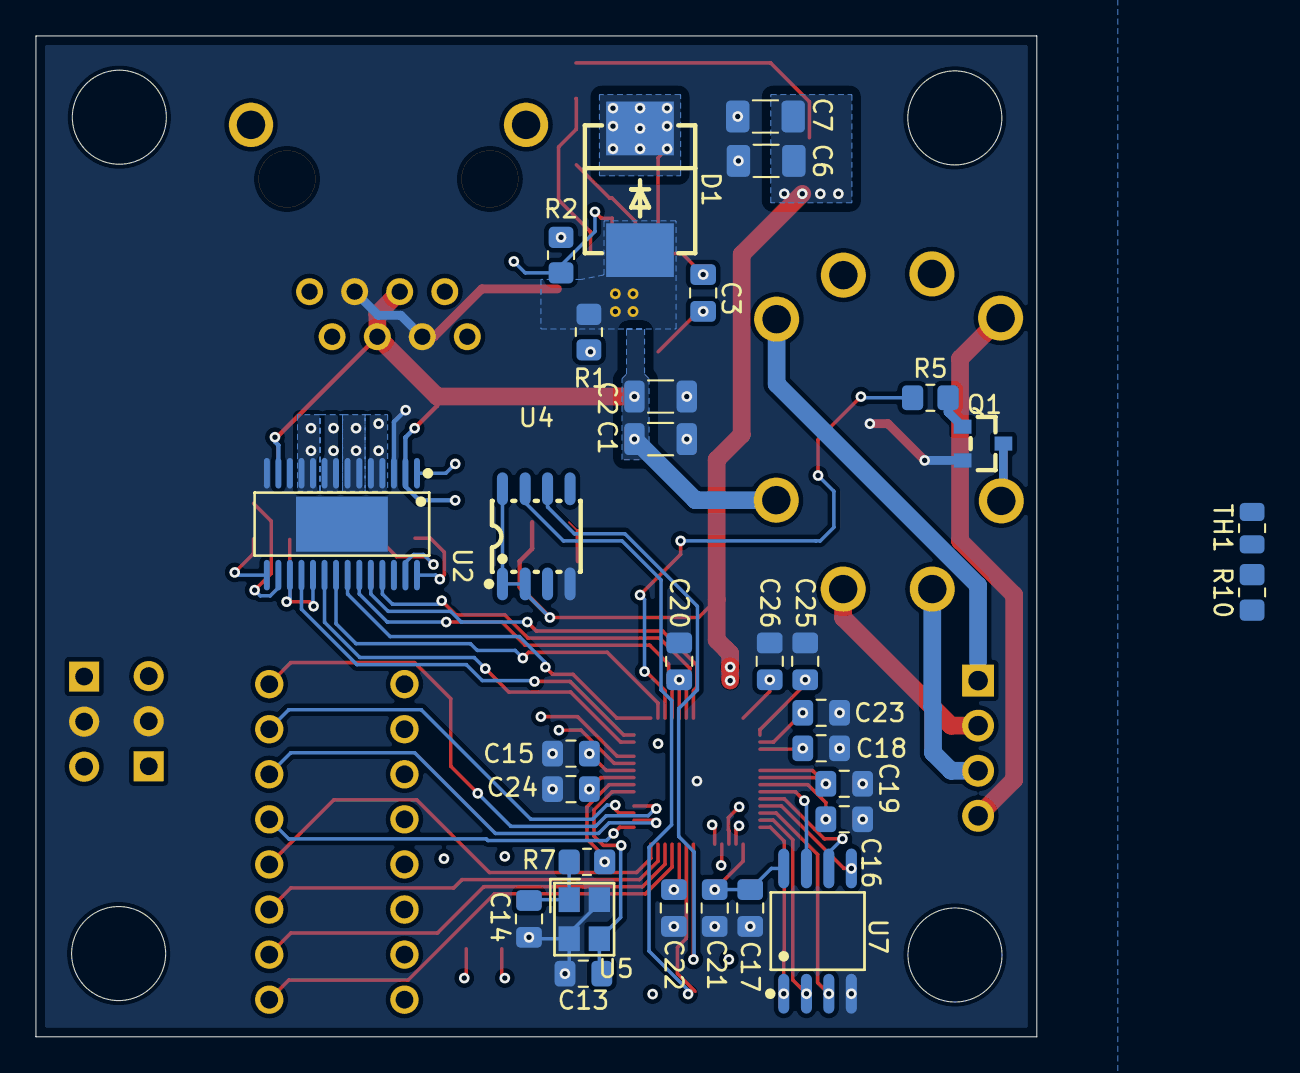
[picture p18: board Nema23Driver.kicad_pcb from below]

Board: 4 copper layers, 56.4 x 56.4 mm, 60 parts (31 on the bottom side), 58 nets.

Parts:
C1, C2: 2.2u; C_1206_3216Metric
C3, C11, C12, C15, C16, C17, C20, C21, C22, C23, C24, C25, C26: 0.1u; C_0805_2012Metric_Pad1.18x1.45mm_HandSolder
C4: 6800p; C_1206_3216Metric
C5: 39p; C_0402_1005Metric_Pad0.74x0.62mm_HandSolder
C6, C7: 47u; C_1206_3216Metric_Pad1.33x1.80mm_HandSolder
C8: 0.022u; C_0805_2012Metric_Pad1.18x1.45mm_HandSolder
C9: 0.22u; C_0805_2012Metric_Pad1.18x1.45mm_HandSolder
C10: 0.47u; C_0805_2012Metric_Pad1.18x1.45mm_HandSolder
C13, C14: 15p; C_0805_2012Metric_Pad1.18x1.45mm_HandSolder
C18, C19: 1u; C_0805_2012Metric_Pad1.18x1.45mm_HandSolder
D1: B560C-13-F; SMC_L7.1-W6.2-LS8.1-RD
H1, H2, H3, H4: MountingHole_Pad; MountingHole_5.3mm_M5
J1, J2: Conn_01x03_Socket; PinHeader_1x03_P2.54mm_Vertical
K1: SRE-24VDC-SL-2C; RELAY-TH_SRE-12VDC-SL-2C
L1: FXL1040-8R2-M; IND-SMD_L11.5-W10.0_FXL1040
M1: Stepper_Motor_bipolar; CONN-TH_DB125-2.54-4P-GN
Q1: AO3400_C2938367; SOT-23_L2.9-W1.3-P1.90-LS2.4-BR
R1: 162k; R_0805_2012Metric_Pad1.20x1.40mm_HandSolder
R2: 13k; R_0805_2012Metric_Pad1.20x1.40mm_HandSolder
R3: 31.6k; R_0805_2012Metric_Pad1.20x1.40mm_HandSolder
R4: 10.2k; R_0805_2012Metric_Pad1.20x1.40mm_HandSolder
R5, R7: 1k; R_0805_2012Metric_Pad1.20x1.40mm_HandSolder
R6: 10k; R_0805_2012Metric_Pad1.20x1.40mm_HandSolder
R8, R9, R10, R11: 5k; R_0805_2012Metric_Pad1.20x1.40mm_HandSolder
RJ1: R-RJ45R10P-B000; RJ45-TH_R-RJ45R10P-B000
SW1: DS-08BLP; SW-TH_16P-L21.9-W9.9-P2.54-LS7.6
TH1, TH2: 10K; R_0805_2012Metric
U1: TPS54360BDDAR; SOIC-8_L5.0-W4.0-P1.27-LS6.0-BL-EP2.0
U2: DRV8434SPWPR; HTSSOP-28_L9.7-W4.4-P0.65-LS6.4-BL-EP-5
U3: PTVS6V0S1UR_C18723426; SOD-123_L2.7-W1.6-LS3.7-RD
U4: MT6701CT-STD-R; SOP-8_L4.9-W3.9-P1.27-LS6.0-BL
U5: ABM8-272-T3_C20625731; CRYSTAL-SMD_4P-L3.2-W2.5-BL
U6: RP2040; LQFN-56_L7.0-W7.0-P0.4-EP
U7: W25Q128JVSIQTR; SOIC-8_L5.3-W5.3-P1.27-LS8.0-BL
U8: SM03B-SRSS-TB(LF)(SN)(P); CONN-SMD_SM03B-SRSS-TB-LF-SN-P

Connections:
+1V1: C15.2, C16.2, C18.2, U6.23 (DVDD), U6.45 (VREG_VOUT), U6.50 (DVDD)
+3.3V: C6.1, C7.1, C11.2, C12.2, C17.2, C19.2, C20.2, C21.2, C22.2, C23.2, C24.2, C25.2, C26.2, L1.2, R3.1, R8.2, R9.1, SW1.1 (PIN1), SW1.2 (PIN2), SW1.3 (PIN3), SW1.4 (PIN4), SW1.5 (PIN5), SW1.6 (PIN6), SW1.7 (PIN7), SW1.8 (PIN8), TH1.2, TH2.2, U2.17 (VREF), U2.19 (VSDO), U3.1 (K), U4.1 (VDD), U4.2 (MODE), U4.8 (Z), U6.1 (IOVDD), U6.10 (IOVDD), U6.22 (IOVDD), U6.33 (IOVDD), U6.42 (IOVDD), U6.43 (ADC_AVDD), U6.44 (VREG_IN), U6.48 (USB_VDD), U6.49 (IOVDD), U7.8 (VCC)
/DIR: U2.24 (DIR), U6.35 (GPIO23)
/EN: U2.25 (ENBLE), U6.34 (GPIO22)
/EN_MOT: R5.1, U6.31 (GPIO20)
/Magnetic Sensor/SCL: R8.1, U4.7 (B), U6.9 (GPIO7)
/Magnetic Sensor/SDA: R9.2, U4.6 (A), U6.8 (GPIO6)
/Motor/A0: K1.6, M1.2 (-)
/Motor/A0.Enabled: K1.8, U2.4 (AOUT1), U2.5 (AOUT1)
/Motor/A1: K1.7, M1.1, U2.6 (AOUT2), U2.7 (AOUT2)
/Motor/B0: K1.3, M1.3
/Motor/B0.Enabled: K1.5, U2.10 (BOUT1), U2.11 (BOUT1)
/Motor/B1: K1.4, M1.4, U2.8 (BOUT2), U2.9 (BOUT2)
/Motor/CS: U2.18 (NSCS), U6.28 (GPIO17)
/Motor/SCLK: U2.22 (SCLK), U6.29 (GPIO18)
/Motor/SDI: U2.21 (SDI), U6.30 (GPIO19)
/Motor/SDO: U2.20 (SDO), U6.27 (GPIO16)
/Power/Dir: RJ1.8, U6.4 (GPIO2)
/Power/FB: R3.2, R4.1, U1.5 (FB)
/Power/Step: RJ1.1, U6.5 (GPIO3)
/RP2040/ADC2: R11.1, TH2.1, U6.40 (GPIO28_ADC2)
/RP2040/ADC3: R10.1, TH1.1, U6.41 (GPIO29_ADC3)
/RP2040/CLK: U6.52 (QSPI_SCLK), U7.6 (CLK)
/RP2040/D0: U6.53 (QSPI_SD0), U7.5 (DI)
/RP2040/D1: U6.55 (QSPI_SD1), U7.2 (DO)
/RP2040/D2: U6.54 (QSPI_SD2), U7.3 (IO2)
/RP2040/D3: U6.51 (QSPI_SD3), U7.7 (IO3)
/RP2040/SS: U6.56 (QSPI_SS), U7.1 (~CS)
/RP2040/UART0_RX: J1.3, U6.3 (GPIO1)
/RP2040/UART0_TX: J1.1, U6.2 (GPIO0)
/STEP: U2.23 (STEP), U6.32 (GPIO21)
/SWCLK: J2.3, U6.24 (SWCLK), U8.1
/SWDIO: J2.1, U6.25 (SWD), U8.3
GND: C1.2, C2.2, C4.2, C5.2, C6.2, C7.2, C10.1, C11.1, C12.1, C13.2, C14.1, C15.1, C16.1, C17.1, C18.1, C19.1, C20.1, C21.1, C22.1, C23.1, C24.1, C25.1, C26.1, D1.2 (A), J1.2, J2.2, Q1.2 (S), R1.2, R4.2, R10.2, R11.2, RJ1.3, RJ1.6, U1.7 (GND), U1.9 (PAD), U2.3 (PGND), U2.12 (PGND), U2.14 (GND), U2.29 (EP), U3.2 (A), U4.4 (GND), U5.2 (GND), U5.4 (GND), U6.57 (GND), U7.4 (GND), U8.2
unnamed: C4.1, R2.2
unnamed: C14.2, R7.1, U5.1
unnamed: C3.2, D1.1 (K), L1.1, U1.8 (SW)
unnamed: K1.1, Q1.3 (D)
unnamed: Q1.1 (G), R5.2
unnamed: SW1.9 (PIN9), U6.11 (GPIO8)
unnamed: SW1.10 (PIN10), U6.12 (GPIO9)
unnamed: SW1.11 (PIN11), U6.13 (GPIO10)
unnamed: SW1.12 (PIN12), U6.14 (GPIO11)
unnamed: SW1.13 (PIN13), U6.15 (GPIO12)
unnamed: SW1.14 (PIN14), U6.16 (GPIO13)
unnamed: C3.1, U1.1 (BOOT)
unnamed: C5.1, R2.1, U1.6 (COMP)
unnamed: R1.1, U1.4 (RT/CLK)
unnamed: C8.2, U2.28 (CPH)
unnamed: C8.1, U2.27 (CPL)
unnamed: C10.2, R6.2, U2.15 (DVDD)
unnamed: C9.2, U2.1 (VCP)
unnamed: R6.1, U2.16 (nFAULT)
unnamed: SW1.15, U6.17 (GPIO14)
unnamed: SW1.16, U6.18 (GPIO15)
unnamed: C13.1, U5.3, U6.20 (XIN)
unnamed: R7.2, U6.21 (XOUT)
VDD: C1.1, C2.1, C9.1, K1.2, RJ1.4, RJ1.5, U1.2 (VIN), U2.2 (VM), U2.13 (VM)

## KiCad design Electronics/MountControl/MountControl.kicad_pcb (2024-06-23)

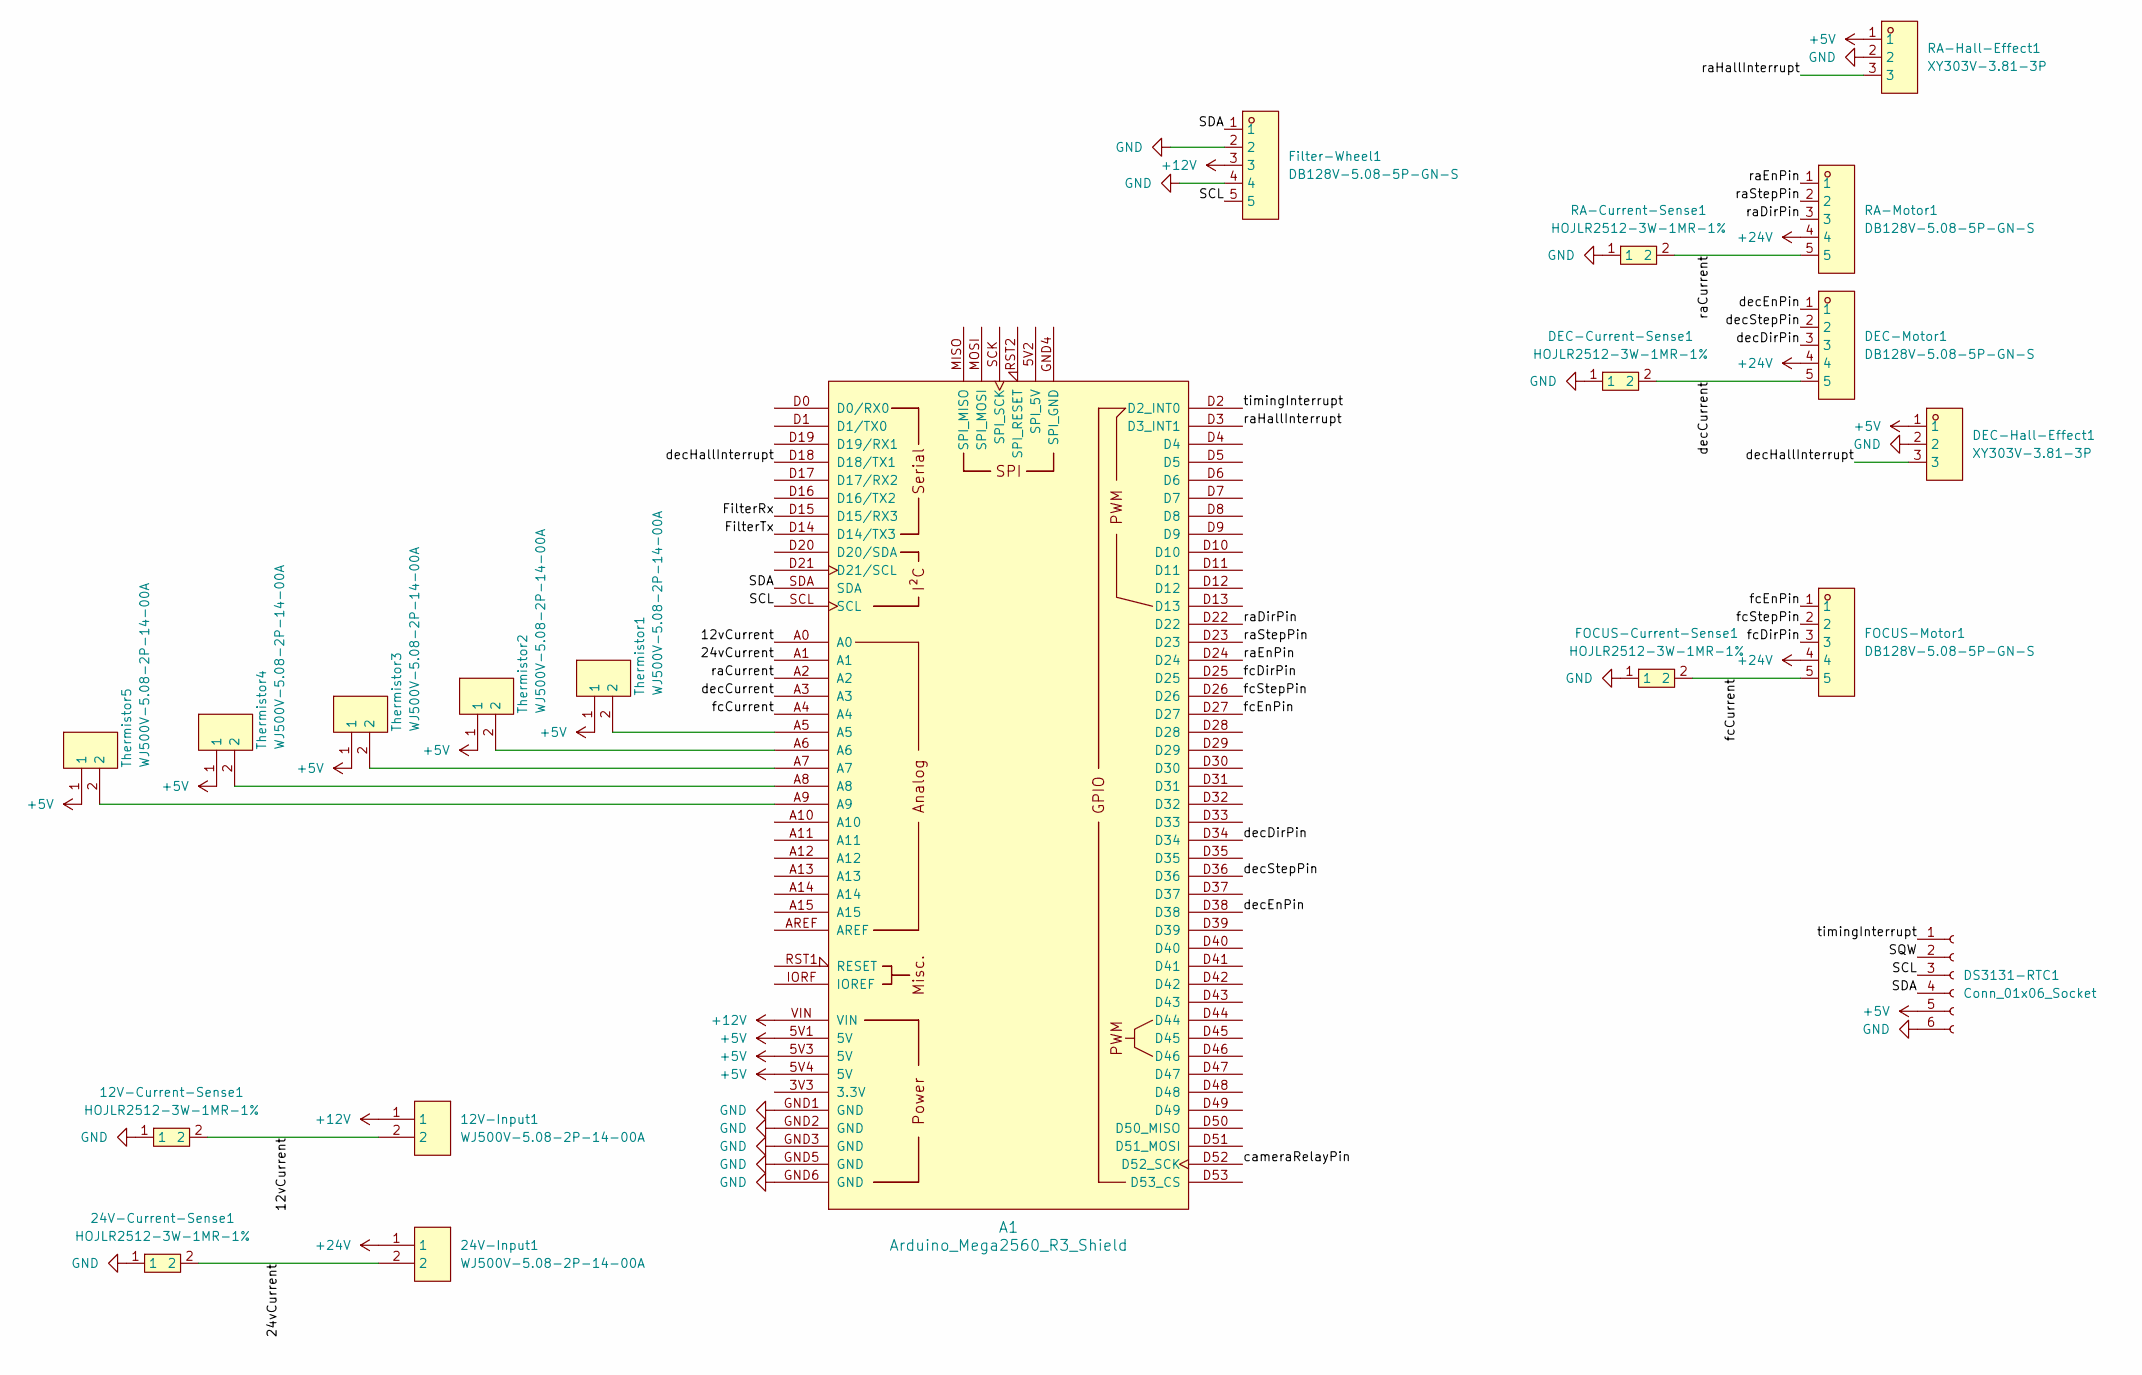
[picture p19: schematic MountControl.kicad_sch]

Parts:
12V-Current-Sense1, 24V-Current-Sense1: HOJLR2512-3W-1MR-1%; RES-SMD_L6.4-W3.2-R2512; LCSC Part C2903470
12V-Input1, 24V-Input1: WJ500V-5.08-2P-14-00A; CONN-TH_2P-P5.00_WJ500V-5.08-2P; LCSC Part C8465
A1: Arduino_Mega2560_R3_Shield
DEC-Current-Sense1: HOJLR2512-3W-1MR-1%; RES-SMD_L6.4-W3.2-R2512; LCSC Part C2903470
DEC-Hall-Effect1: XY303V-3.81-3P; CONN-TH_XY303V-3.81-3P; LCSC Part C557684
DEC-Motor1: DB128V-5.08-5P-GN-S; CONN-TH_5P-P5.08_DIBO_DB128V-5.08-5P-GN-S; LCSC Part C2927513
DS3131-RTC1: Conn_01x06_Socket; PinHeader_1x06_P2.54mm_Horizontal
FOCUS-Current-Sense1: HOJLR2512-3W-1MR-1%; RES-SMD_L6.4-W3.2-R2512; LCSC Part C2903470
FOCUS-Motor1: DB128V-5.08-5P-GN-S; CONN-TH_5P-P5.08_DIBO_DB128V-5.08-5P-GN-S; LCSC Part C2927513
Filter-Wheel1: DB128V-5.08-5P-GN-S; CONN-TH_5P-P5.08_DIBO_DB128V-5.08-5P-GN-S; LCSC Part C2927513
RA-Current-Sense1: HOJLR2512-3W-1MR-1%; RES-SMD_L6.4-W3.2-R2512; LCSC Part C2903470
RA-Hall-Effect1: XY303V-3.81-3P; CONN-TH_XY303V-3.81-3P; LCSC Part C557684
RA-Motor1: DB128V-5.08-5P-GN-S; CONN-TH_5P-P5.08_DIBO_DB128V-5.08-5P-GN-S; LCSC Part C2927513
Thermistor1, Thermistor2, Thermistor3, Thermistor4, Thermistor5: WJ500V-5.08-2P-14-00A; CONN-TH_2P-P5.00_WJ500V-5.08-2P; LCSC Part C8465

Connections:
+5V: A1.5V1 (5V), A1.5V3 (5V), A1.5V4 (5V), DEC-Hall-Effect1.1, DS3131-RTC1.5, RA-Hall-Effect1.1, Thermistor1.1, Thermistor2.1, Thermistor3.1, Thermistor4.1, Thermistor5.1
+12V: 12V-Input1.1, A1.VIN, Filter-Wheel1.3
+24V: 24V-Input1.1, DEC-Motor1.4, FOCUS-Motor1.4, RA-Motor1.4
/12vCurrent: 12V-Current-Sense1.2, 12V-Input1.2, A1.A0
/24vCurrent: 24V-Current-Sense1.2, 24V-Input1.2, A1.A1
/FilterRx: A1.D15 (D15/RX3)
/FilterTx: A1.D14 (D14/TX3)
/SCL: A1.SCL, DS3131-RTC1.3, Filter-Wheel1.5
/SDA: A1.SDA, DS3131-RTC1.4, Filter-Wheel1.1
/SQW: DS3131-RTC1.2
/cameraRelayPin: A1.D52 (D52_SCK)
/decCurrent: A1.A3, DEC-Current-Sense1.2, DEC-Motor1.5
/decDirPin: A1.D34, DEC-Motor1.3
/decEnPin: A1.D38, DEC-Motor1.1
/decHallInterrupt: A1.D18 (D18/TX1), DEC-Hall-Effect1.3
/decStepPin: A1.D36, DEC-Motor1.2
/fcCurrent: A1.A4, FOCUS-Current-Sense1.2, FOCUS-Motor1.5
/fcDirPin: A1.D25, FOCUS-Motor1.3
/fcEnPin: A1.D27, FOCUS-Motor1.1
/fcStepPin: A1.D26, FOCUS-Motor1.2
/raCurrent: A1.A2, RA-Current-Sense1.2, RA-Motor1.5
/raDirPin: A1.D22, RA-Motor1.3
/raEnPin: A1.D24, RA-Motor1.1
/raHallInterrupt: A1.D3 (D3_INT1), RA-Hall-Effect1.3
/raStepPin: A1.D23, RA-Motor1.2
/timingInterrupt: A1.D2 (D2_INT0), DS3131-RTC1.1
GND: 12V-Current-Sense1.1, 24V-Current-Sense1.1, A1.GND1 (GND), A1.GND2 (GND), A1.GND3 (GND), A1.GND5 (GND), A1.GND6 (GND), DEC-Current-Sense1.1, DEC-Hall-Effect1.2, DS3131-RTC1.6, FOCUS-Current-Sense1.1, Filter-Wheel1.2, Filter-Wheel1.4, RA-Current-Sense1.1, RA-Hall-Effect1.2
unnamed: A1.A5, Thermistor1.2
unnamed: A1.A6, Thermistor2.2
unnamed: A1.A7, Thermistor3.2
unnamed: A1.A8, Thermistor4.2
unnamed: A1.A9, Thermistor5.2


Board: 4 copper layers, 194.1 x 115.6 mm, 20 parts (0 on the bottom side), 28 nets.

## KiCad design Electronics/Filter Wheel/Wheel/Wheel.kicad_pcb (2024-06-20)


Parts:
A1: Arduino_UNO_R3
A2: Pololu_Breakout_A4988; Pololu_Breakout-16_15.2x20.3mm
P1, P2: WJ500V-5.08-2P-14-00A; CONN-TH_2P-P5.00_WJ500V-5.08-2P; LCSC Part C8465
U1, U2, U3, U4, U5, U6, U7, U8, U9: SS361CT; SOT-23-3_L2.9-W1.3-P1.90-LS2.4-BR; LCSC Part C396072
U10: MX128-2.54-04P-GN01-CU-Y-A; CONN-TH_4P-P2.54_MX128-2.54-GN01-04P-CU-Y-A; LCSC Part C5188444

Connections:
+5V: A1.5 (+5V), A2.2 (VDD), A2.10 (MS1), A2.11 (MS2), A2.12 (MS3)
/SCL: A1.14 (SCL/A5), P2.2
/SDA: A1.13 (SDA/A4), P2.1
GND: A1.6 (GND), A1.7 (GND), A1.29 (GND), P1.2, U1.3 (GND(-)), U2.3 (GND(-)), U3.3 (GND(-)), U4.3 (GND(-)), U5.3 (GND(-)), U6.3 (GND(-)), U7.3 (GND(-)), U8.3 (GND(-)), U9.3 (GND(-))
unnamed: A1.17 (D2), U1.2 (OUTPUT)
unnamed: A1.18 (D3), U2.2 (OUTPUT)
unnamed: A1.19 (D4), U3.2 (OUTPUT)
unnamed: A1.20 (D5), U4.2 (OUTPUT)
unnamed: A1.21 (D6), U5.2 (OUTPUT)
unnamed: A1.22 (D7), U6.2 (OUTPUT)
unnamed: A1.23 (D8), U7.2 (OUTPUT)
unnamed: A1.24 (D9), U8.2 (OUTPUT)
unnamed: A1.25 (D10), U9.2 (OUTPUT)
unnamed: A1.26 (D11), A2.16 (DIR)
unnamed: A1.27 (D12), A2.15 (STEP)
unnamed: A1.28 (D13), A2.9 (~ENABLE)
unnamed: A2.4 (1A), U10.2
unnamed: A2.3 (1B), U10.1
unnamed: A2.5 (2A), U10.3
unnamed: A2.6 (2B), U10.4
VCC: A1.8 (VIN), A2.8 (VMOT), P1.1, U1.1 (VCC(+)), U2.1 (VCC(+)), U3.1 (VCC(+)), U4.1 (VCC(+)), U5.1 (VCC(+)), U6.1 (VCC(+)), U7.1 (VCC(+)), U8.1 (VCC(+)), U9.1 (VCC(+))

Board: 2 copper layers, 14 parts (0 on the bottom side), 21 nets, no tracks yet.

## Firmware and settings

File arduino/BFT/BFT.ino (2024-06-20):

#include <DS3231.h>
DS3231 RTC;



//RTC Pins
const uint8_t timingInterruptPin = 2; //Hardware interrupt 4
//Hall Effect Sensor Pins
const uint8_t eqHallInterruptPin = 3;//Eq
const uint8_t decHallInterruptPin = 18;//Dec
//DEC Stepper Pins
const uint8_t decEnPin = 38;// Enable 22
const uint8_t decStepPin = 36;// Step 24
const uint8_t decDirPin = 34;// Direction 26
//EQ Stepper Pins
const uint8_t eqEnPin = 24;// Enable 23
const uint8_t eqStepPin = 23;// Step 25
const uint8_t eqDirPin = 22;// Direction 27
//Focus Stepper Pins
const uint8_t fcEnPin = 27;//Enable   36
const uint8_t fcStepPin = 26;//Step  34
const uint8_t fcDirPin = 25;//Direction 32
//Camera Power Disable Pin 37
const uint8_t cameraPowerPin = 52; //Camera Relay is Normally Closed.

//Serial communication variables
String serialCommand;
bool commandFinished = false;

int pulsesReceived = 0;
bool secondaryPulseCount = false;
int stepsTaken = 0;



long currentEqSteps = 0;
long maxEqSteps = 446900;

long currentDecSteps = 0;
long maxDecSteps = 223448;


void setup() {
  initializeSerialInterfaces();
  initializePinDirections();
  initializeInterruptInterfaces();
  initializeRTCModule();
  initializeAxisMotors();
}

void loop() {
  checkCommandFinished();
}




void serialEvent() {
  while (Serial.available()){
    char inChar = (char)Serial.read();
    serialCommand += inChar;
    if (inChar == ';'){
      commandFinished = true;
    }
  }
}



void initializeSerialInterfaces(){
  //Begin Serial Interfaces
  Serial.begin(115200);
  Wire.begin();
  delay(1);
  Serial.println("Serial Initialized");
}
void initializeRTCModule(){  
  RTC.enable32kHz(true);
  Serial.println("RTC Initialized");
}
void initializePinDirections(){
  //declination axis
  pinMode(decEnPin, OUTPUT);
  pinMode(decStepPin, OUTPUT);
  pinMode(decDirPin, OUTPUT);
  //equitorial axis
  pinMode(eqEnPin, OUTPUT);
  pinMode(eqStepPin, OUTPUT);
  pinMode(eqDirPin, OUTPUT);
  //focus control axis
  pinMode(fcEnPin, OUTPUT);
  pinMode(fcStepPin, OUTPUT);
  pinMode(fcDirPin, OUTPUT);
  //camera power control 
  pinMode(cameraPowerPin, OUTPUT);
  //interrupt pins
  pinMode(timingInterruptPin, INPUT);
  pinMode(eqHallInterruptPin, INPUT);
  pinMode(decHallInterruptPin, INPUT);
  Serial.println("Interface Pins Initialized");
}
void initializeInterruptInterfaces(){
  attachInterrupt(digitalPinToInterrupt(timingInterruptPin), trackingInterrupt, RISING);
}
void initializeAxisMotors(){
  digitalWrite(eqEnPin, HIGH);
  digitalWrite(decEnPin, HIGH);
  Serial.println("Motor output Enabled");
}
void checkCommandFinished(){
  if (commandFinished){
    executeCommand(serialCommand);
    clearCommand();
  }
}



void trackingInterrupt(){
  pulsesReceived += 1;
  if (pulsesReceived == 1514 && !secondaryPulseCount){
      stepsTaken += 1;
    if (stepsTaken == 48){
      stepsTaken = 0;
      secondaryPulseCount = !secondaryPulseCount;
    }
    moveEqAxis(1, false);
    pulsesReceived = 0;
  }
  else if (pulsesReceived == 1513 && secondaryPulseCount){
    stepsTaken += 1;
    if (stepsTaken == 48){
      stepsTaken = 0;
      secondaryPulseCount = !secondaryPulseCount;
    }
    moveEqAxis(1, false);
    pulsesReceived = 0;
  }
}

void executeCommand(String command){
  Serial.println("Receiving Manual Update Command. Disabling RTC Interrupt Pulses");
  RTC.enable32kHz(false);
  String commandType = command.substring(0,1);
  long movement = command.substring(1).toInt();
  bool direction = (movement > 0);
  long steps = arcSecsToSteps(abs(movement));
  String dir = String("LOW");
  if (direction){
    dir = String("HIGH");
  }
  if(commandType == "D"){
    Serial.println("Declination Axis Move: "+ String(steps) +", Direction: "+String(dir));
    moveDecAxis(steps, direction);
  }
  if(commandType == "E"){
    Serial.println("Equitorial Axis Move: "+ String(steps)+", Direction: "+String(dir));
    moveEqAxis(steps, direction);
  }
  if(commandType == "F"){
    Serial.println("Focus Move: "+ String(movement)+", Direction: "+String(dir));
    moveFcAxis(abs(movement), direction);
  }
  if(commandType == "G"){
    Serial.println("Interpreting General Command");
    executeGeneralCommand(movement);
   }
  Serial.println("Finished Mnual Command, Enabling RTC Interrupt Pulses");
  RTC.enable32kHz(true);
}



void clearCommand(){
  serialCommand = "";
  commandFinished = false;
}

void moveEqAxis(long steps, bool direction){
  digitalWrite(eqDirPin, direction);
  long i = 0;
  while (i < steps){
    if(abs(currentEqSteps) <= maxEqSteps){
      digitalWrite(eqStepPin, HIGH);
      delayMicroseconds(160);
      digitalWrite(eqStepPin, LOW);
      delayMicroseconds(160);
      if(direction){
        currentEqSteps += 1;
      }else{
        currentEqSteps -= 1;
      }
      i++;
    }else{
      i = steps;
      Serial.println("End of ability to move on Equitorial Axis. Unable to Move Further.");
    }
  }
  if(steps > 1){
    Serial.println("Completed Equitorial Move. Current Pos: "+String(currentEqSteps));
  }
}

void moveDecAxis(long steps, bool direction){
  digitalWrite(decDirPin, direction);
  long i = 0;
  while (i < steps){
    if(abs(currentDecSteps) <= maxDecSteps){
      digitalWrite(decStepPin, HIGH);
      delayMicroseconds(160);
      digitalWrite(decStepPin, LOW);
      delayMicroseconds(160);
      if(direction){
        currentDecSteps += 1;
      }else{
        currentDecSteps -= 1;
      }
      i++;
    }else{
      i = steps;
      Serial.println("End of ability to move on Declination Axis. Unable to Move Further.");
    }
  }
  if(steps > 1){
    Serial.println("Completed Declination Move. Current Pos: "+ String(currentDecSteps));
  }
}

void moveFcAxis(long steps, bool direction){
  digitalWrite(fcEnPin, HIGH);
  digitalWrite(fcDirPin, direction);
  long i = 0;
  while (i < steps){
    digitalWrite(fcStepPin, HIGH);
    delayMicroseconds(160);
    digitalWrite(fcStepPin, LOW);
    delayMicroseconds(160);
    i++;
  }
  digitalWrite(fcEnPin, LOW);
}
void executeGeneralCommand(long commandCode){
  if (commandCode == 1){
    Serial.println("RESETTING CAMERA");
    digitalWrite(cameraPowerPin, HIGH);
    delay(5000);
    digitalWrite(cameraPowerPin, LOW);
  }
  if (commandCode == 2){
    Serial.println("Disabling RTC Pulses");
    RTC.enable32kHz(false);
  }
  if (commandCode == 3){
    Serial.println("Enabling RTC Pulses");
    RTC.enable32kHz(true);
  }
}

long arcSecsToSteps(long arcSeconds){
  const double arcSecondsPerStep = 0.725;
  long steps = arcSeconds / arcSecondsPerStep;
  return steps;
}

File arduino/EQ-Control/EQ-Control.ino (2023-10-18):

#include <SPI.h>
#include <DRV8434S.h>
#include <DS3231.h>

DS3231 RTC;
DRV8434S RightAscensionStepperDriver;
DRV8434S DeclinationStepperDriver;


const uint8_t RightAscensionChipSelectPin = 5;
const uint8_t DeclinationChipSelectPin = 4;
const uint8_t interruptPin = 2;

const float ArcSecondsPerStep = 0.253125;


const uint32_t smallInterruptCountPerCycle = 5525;
const int smallInterruptMaxCycles = 162;

const uint32_t  largeInterruptCountPerCycle = 5535;
const int maxInterruptCycles = 300;

int currentCycle = 0;
int currentInterruptCount = 0;


String MovementCommand = "";
bool CommandFinishedReceiving = false;

bool RightAscensionReverseEnabled = false;
bool DeclinationReverseEnabled = false;

bool TakingAdjustmentSteps = false;

int RightAscensionStandbyCurrent = 2000;
int RightAscensionSlewingCurrent = 2000;

int DeclinationStandbyCurrent = 500;
int DeclinationSlewingCurrent = 2000;





void setup(){
  Serial.begin(115200);
  Wire.begin();
  SPI.begin();
  delay(1);

  Serial.println("Mount is initializing");
  MovementCommand.reserve(200);
  
  RightAscensionStepperDriver.setChipSelectPin(RightAscensionChipSelectPin);
  DeclinationStepperDriver.setChipSelectPin(DeclinationChipSelectPin);
  pinMode(interruptPin, INPUT);
  attachInterrupt(digitalPinToInterrupt(interruptPin), countCycles, CHANGE);
  delay(1);

  RightAscensionStepperDriver.resetSettings();
  RightAscensionStepperDriver.clearFaults();
  RightAscensionStepperDriver.setCurrentMilliamps(RightAscensionStandbyCurrent);
  Serial.println("Right Driver Ascension Reset, Faults Cleared, Max Current Set");
  DeclinationStepperDriver.resetSettings();
  DeclinationStepperDriver.clearFaults();
  DeclinationStepperDriver.setCurrentMilliamps(DeclinationStandbyCurrent);
  Serial.println("Declination Driver Reset, Faults Cleared, Max Current Set");


  RightAscensionStepperDriver.enableSPIDirection();
  RightAscensionStepperDriver.enableSPIStep();
  Serial.println("Right ascension driver SPI controle enabled");
  DeclinationStepperDriver.enableSPIDirection();
  DeclinationStepperDriver.enableSPIStep();
  Serial.println("Declination driver SPI control enabled");


  RightAscensionStepperDriver.enableDriver();
  DeclinationStepperDriver.enableDriver();
  Serial.println("Motor output enabled.");


  RightAscensionStepperDriver.setStepMode(DRV8434SStepMode::MicroStep128);
  DeclinationStepperDriver.setStepMode(DRV8434SStepMode::MicroStep128);
  RightAscensionStepperDriver.setDirection(RightAscensionReverseEnabled);

  Serial.println("Mount initialization complete.");
  RTC.enable32kHz(true);
}





void loop(){
  if (CommandFinishedReceiving) {
    executeCommand(MovementCommand);
    clearCommand();
  }
  
}




void countCycles(){
  currentInterruptCount += 1;
  if(currentCycle < smallInterruptMaxCycles && currentInterruptCount == smallInterruptCountPerCycle){
    makeTrackingStep();
    currentCycle += 1; 
    currentInterruptCount = 0;
  }else if(currentCycle >=smallInterruptMaxCycles && currentCycle < maxInterruptCycles && currentInterruptCount == largeInterruptCountPerCycle){
    makeTrackingStep();
    currentCycle += 1;
    currentInterruptCount = 0;
  }
  if(currentCycle == maxInterruptCycles){
    currentCycle = 0;
    Serial.println("Cycle Reset");
  }

  
}



void makeTrackingStep(){
  noInterrupts();
  for (int i = 0; i < 5; i++){
    RightAscensionStepperDriver.step();
    delayMicroseconds(10);
  }
  interrupts();
}





void serialEvent() {
  while (Serial.available()) {
    char inChar = (char)Serial.read();
    MovementCommand += inChar;
    if (inChar == '\r') {
      CommandFinishedReceiving = true;
    }
  }
}





void executeCommand(String command){
  noInterrupts();
  int DeclinationIndex = command.indexOf(";");

  String RightAscensionMovementText = command.substring(0, DeclinationIndex);
  String DeclinationMovementText = command.substring(DeclinationIndex+1, command.length()-1);

  long RightAscensionMovement = RightAscensionMovementText.toInt();
  long DeclinationMovement = DeclinationMovementText.toInt();
  
  bool RightAscensionDirection = RightAscensionMovement > 0;
  if(!RightAscensionReverseEnabled){RightAscensionDirection = RightAscensionDirection;}
  bool DeclinationDirection = DeclinationMovement > 0;
  if(!DeclinationReverseEnabled){DeclinationDirection = DeclinationDirection;}

  RightAscensionMovement = abs(RightAscensionMovement);
  DeclinationMovement = abs(DeclinationMovement);

  long RightAscensionSteps = arcSecondsToSteps(RightAscensionMovement);
  long DeclinationSteps = arcSecondsToSteps(DeclinationMovement);
  
  Serial.println("Starting RA Movement");
  RightAscensionStepperDriver.setCurrentMilliamps(RightAscensionSlewingCurrent);
  RightAscensionStepperDriver.setDirection(RightAscensionDirection);
  for ( long i = 0; i < RightAscensionSteps; i++){
    RightAscensionStepperDriver.step();
    delayMicroseconds(10);
  }
  RightAscensionStepperDriver.setDirection(RightAscensionReverseEnabled);
  RightAscensionStepperDriver.setCurrentMilliamps(RightAscensionStandbyCurrent);
  Serial.println("Finished RA Movement");
  

  Serial.println("Starting DEC Movement");
  DeclinationStepperDriver.setCurrentMilliamps(DeclinationSlewingCurrent);
  DeclinationStepperDriver.setDirection(DeclinationDirection);
  for (long i = 0; i < DeclinationSteps; i++){
    DeclinationStepperDriver.step();
    delayMicroseconds(10);
  }
  DeclinationStepperDriver.setCurrentMilliamps(DeclinationStandbyCurrent);
  Serial.println("Finished DEC Movement");
  currentCycle = 0;
  currentInterruptCount = 0;
  interrupts();
}





void clearCommand(){
  MovementCommand = "";
  CommandFinishedReceiving = false;
}





long arcSecondsToSteps(long arcSeconds){
  return long(arcSeconds/ArcSecondsPerStep);
}

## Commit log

2023-09-29 †eest
2023-10-02 Switched back to /256
2023-10-02 RTC 32K Tracking
    The DS3231 RTC tracks time extremely well.
    Now, instead of relying on a baseless assumption of time, we will use an exact whole number of pulses.
    We know that for MicroStep1/128, we need to take exactly 100 steps every 25.3125 Seconds.
    We receive 65,536 signals per second (on/off) from our RTC.
    So, we take 60 steps, timed at 16, 588 changes to our interrupt pin.
    And 40 steps, timed at 16,590 changes to our interrupt pin.
    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
2023-10-02 Added Schematic For Motor Driver Layout
2023-10-02 Replaced Schematic
2023-10-02 Added Gerber FIles
    [Drill_PTH_Through.DRL, Drill_PTH_Through_Via.DRL, Gerber_BoardOutlineLayer.GKO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]
2023-10-02 Update README.md
    Added Schematic and Images
2023-10-03 Cycle Tracking - Movements
    Stop counting cycles, and reset cycles once updates have been completed.
    [EQ-Control.ino]
2023-10-03 Added Interrupt skipping.
2023-10-04 Added description of how the mount tracks movement.
2023-10-05 Updated Earths Rotational Speed
    No longer 1 Arcsec/Sec(WRONG)
    Now 15 ArcSec/Sec.
    [EQ-Control.ino]
2023-10-06 These camands are trash, but should work with a functional mount
2023-10-06 Moved Turn on Of 32K Pin
    Moved to end of initialization, so it can continue.
2023-10-07 Added Current Limiting to Reduce Temperatures.
2023-10-07 Set Current Back To MAx
2023-10-08 Print out result
2023-10-09 Working on the flow.
2023-10-11 Changed Motor CS Pin
2023-10-15 Removed empty print line.
2023-10-15 First Push
    [Worm Gear.3mf]
2024-05-14 Initializing motors, adding feedback to serial.
2024-06-20 First push of mount controller project.
    [MountControl.kicad_pcb, MountControl.kicad_sch]
2024-06-20 First push.
    [MountControl.kicad_pcb, MountControl.kicad_sch]
2024-06-20 Schematic Finished
    [MountControl.kicad_sch]
2024-06-22 Finished with routing.
    [MountControl.kicad_pcb, MountControl.kicad_sch]
2024-06-23 Added production files
    [MountControl.kicad_pcb, bom.csv, designators.csv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]
2024-10-10 Working on stepper driver
    [Magnetic Sensor.kicad_sch, Motor.kicad_sch, Nema23Driver.kicad_pcb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]
2024-10-13 Working on Pico Control
    [POWER.kicad_sch, PicoControl.kicad_pcb, PicoControl.kicad_sch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]
2024-11-16 Added Correct pin numbers.
    [main.c]
2024-11-26 Updated PCB to Include Hall Sensors
    [PicoControl.kicad_pcb, PicoControl.kicad_sch, bom.csv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]
2024-12-10 Added Homing
2025-03-02 Started working on driver.
    [Driver.kicad_pcb, Driver.kicad_sch]
2025-03-03 Added driver PCB
    [Driver.kicad_pcb, Driver.kicad_sch, bom.csv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]
2025-03-03 Fixed 3D VIew
    [Driver.kicad_pcb]
2025-03-03 Added magnetic encoder
    [MagneticEncoder.kicad_pcb, MagneticEncoder.kicad_sch, bom.csv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]
2025-03-04 Revert "Changed mode to software trigger."
    This reverts commit 70d6acb8dd04d026f04fa6ff50efd9beda5d8489.
    [toupCapture.py, toupcam.py]
2025-03-27 Updated driver PCB
    [Driver.kicad_pcb, Driver.kicad_sch, bom.csv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]
